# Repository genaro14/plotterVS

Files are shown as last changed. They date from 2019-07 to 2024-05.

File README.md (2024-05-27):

# plotterVS
This repository documents Pen plotter desing and usage.

## Background

I´ve been using DIY pen plotters for a while, 3d printed mostly, they were a lot of fun, but those lack of being reliable. This model it's my 2nd iteration trying to solve that issue and wanting to get a good quality final product, based on my particular needs and understanding of the "best" desing that fits the purpose but keeping the costs as low as possible. 
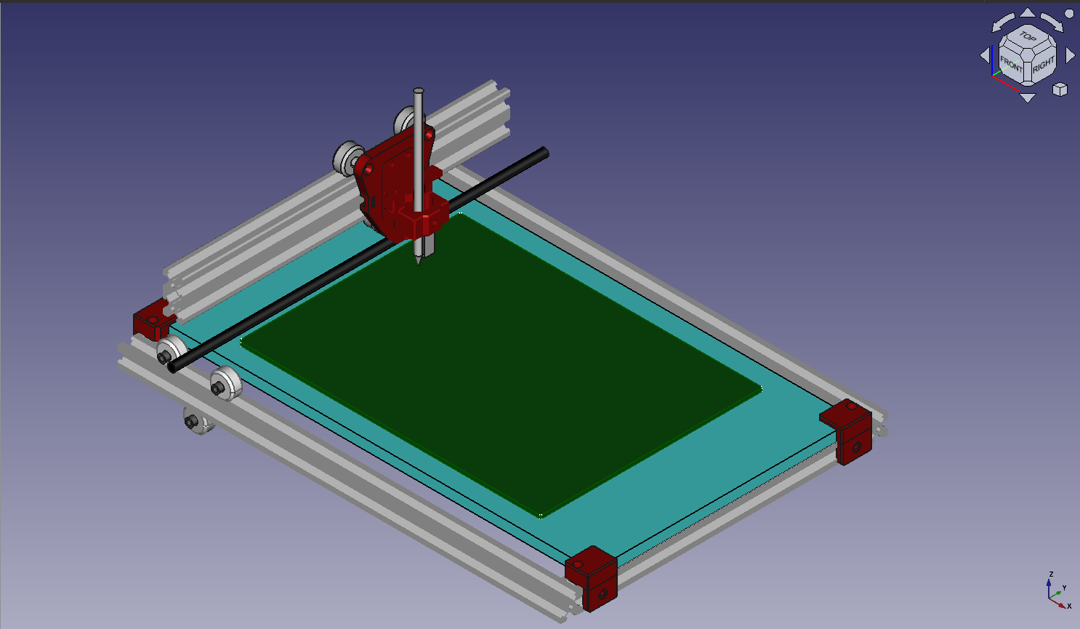
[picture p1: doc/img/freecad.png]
Desing


## How to - BASICS

You will convert a vector ( .SVG ) file to something the plotter can understand, a set of instructions listed in an .Gcode file.

`SVG >>> GCODE`

With a tool like: [SVG2GCODE](https://sameer.github.io/svg2gcode/), you can parse svg files to gcode.     
[Settings JSON file](./Plotter/clean/svg2gcode/svg2gcode_settings.json)   

See below fot templates.(SVG Templates)

Once the gcode file is ready you will send it to plotter. I won't go deeper in this subject.    
Plug >> Connect >> send the file and start it. Check each program docs for details.

Control software examples:
+ Universal Gcode Sender. [UGS](https://winder.github.io/ugs_website/) 
+ CNCJS [cncjs](https://cnc.js.org/)
+ GRBL- Plotter
+ Candle
+ Bcnc

Personally, I've been using the CNCJs over a Raspberry so i don´t need to wire my laptop, it's based on web interface and has proven to be stable and perfectly functional.

## SVG Templates
Some templates can be found in the this [folder](./Plotter/clean/templates).

## Part list for A4 size:
* 2040 vslot: x1 285mm
* 2020 vslot: x2 285mm, .x2 440mm
* Aluminum Corners: x4
* V wheels 22mm: x9 
* Wheel spacers: x6
* Eccentric nuts: x3
* Bolts & T Nuts: At least 12 each
* Gt2 pulleys: 1x 5mm, 2x 8mm
* Gt2 belt. 2 x 500mm, 1 x 600mm
* Gt2 freewheel. 3mm
* 8mm rod, at least 360mm
* Motors Nema 17 x2
* Servo G90
* Aruino Nano & Nanoshield CNC clone with A4988 drivers  (see below)
* Glass: 285 x 440 x 6mm (tempered would be better, but it's expensive, wood can be used too)

Firmware: [GRBL Servo by Misan](https://github.com/misan/grbl-servo) or Robottini's [GRBL Servo](https://github.com/robottini/grbl-servo).

Arduino case: [Link](https://www.thingiverse.com/thing:2379541)

Pen Holder: [Link](https://www.thingiverse.com/thing:3810653/files)

Desing [Freecad Files](./Plotter/2024/2024_complete.FCStd)

## Code Snippets
Code repository for plotting
### Python 
+ Fake cyrcle   
[Circle of Lines](./code/python/fakeCircle/fakeCircle.md).
+ L Systems   
[Lindenmayer Systems](./code/python/lindenmayerSystems/lindenmayerSystems.md)

## JS
+ ARchimendian Spirals    
[Triangle](./code/js/walk/Archimedian_forms/triangle.js)    
[Hexagon](./code/js/walk/Archimedian_forms/hexagon.js)    

### GRBL SERVO SETUP

[Library CODE](https://github.com/robottini/grbl-servo).
  GRBL 0.9i with servo motor support.     
  **Use the PIN D11 to drive the servo.**     
  Use the commands `M03 Sxxx` (xxx between 0 and 255) to rotate the servo between 0-180. The command ``M05`` turn the servo to zero degrees.
  On the current configuration for this build. `M03 S30` is enough for lifting the pen up and clearing the page.
  Commands `M3` and `M5` are valid too.   

| Code | Action  |
|---|---|
| M05 | Pen Down|
| M3 S30 | Pen Up  |

Example configuration can be found on:
[GRBL config](./Plotter/clean/grbl/grbl_config.md)
See below details to map proper pins

### Nanoshield Clone Fixes 
The cheapest controller board on hand was a Keyes Nanoshield clone that supports Arduino nano but it needs some work to work properly.

Soldering required!   
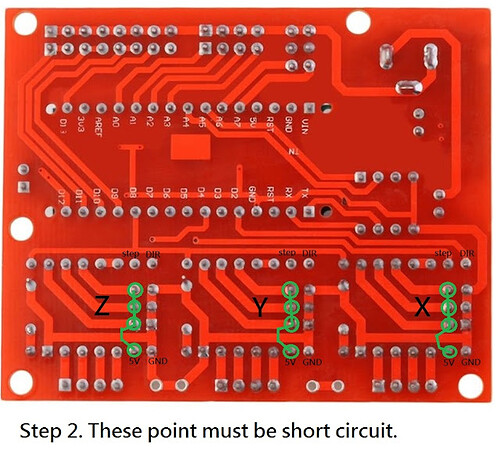
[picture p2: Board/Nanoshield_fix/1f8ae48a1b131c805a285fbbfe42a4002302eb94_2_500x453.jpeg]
Hardware
.    
Also before uploading GRBL to the board, the file 'cpu_map_atmega328.p' has to be modified or replaced.   
Grbl patch [here](./Board/Nanoshield_fix/cpu_map_atmega328p.h)    
Full details from [Instructables](https://www.instructables.com/Fix-Cloned-Arduino-NANO-CNC-Shield/)

## Results 
Cncjs Example and result:
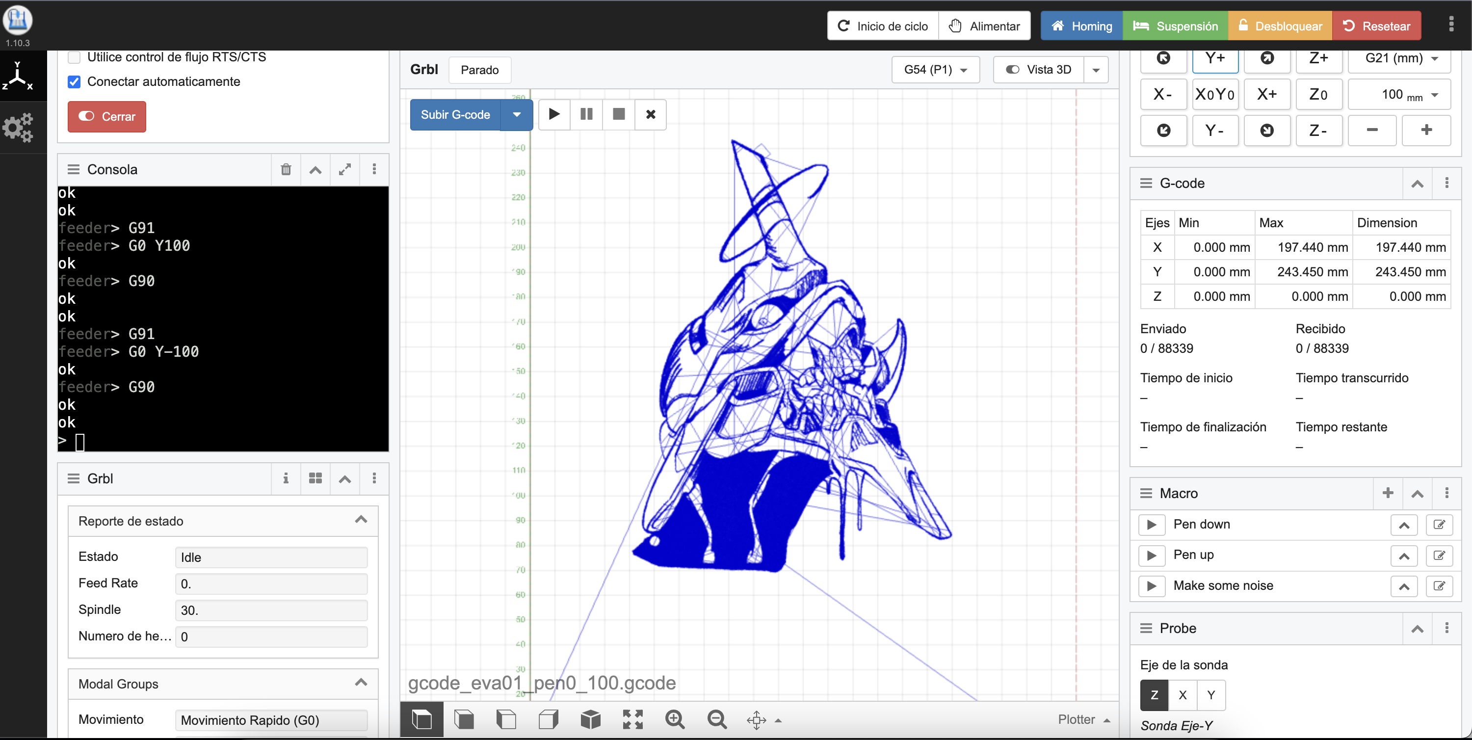
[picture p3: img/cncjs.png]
cncJs
 
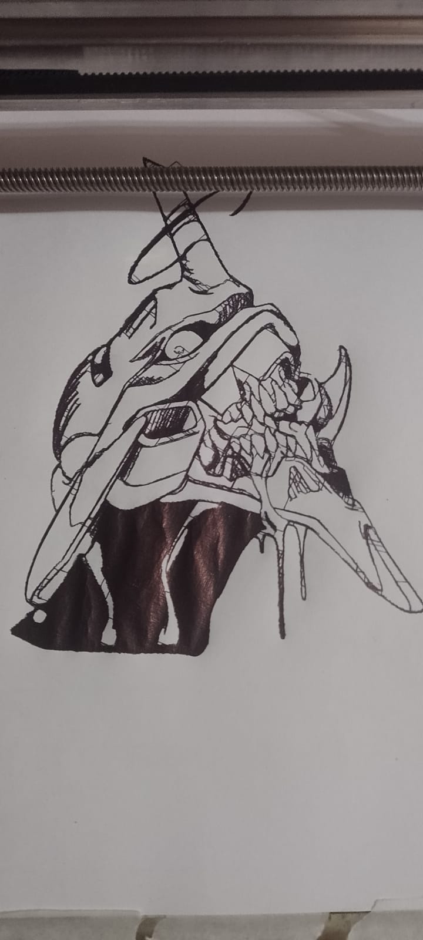
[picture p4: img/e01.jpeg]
eva
        

### Other:
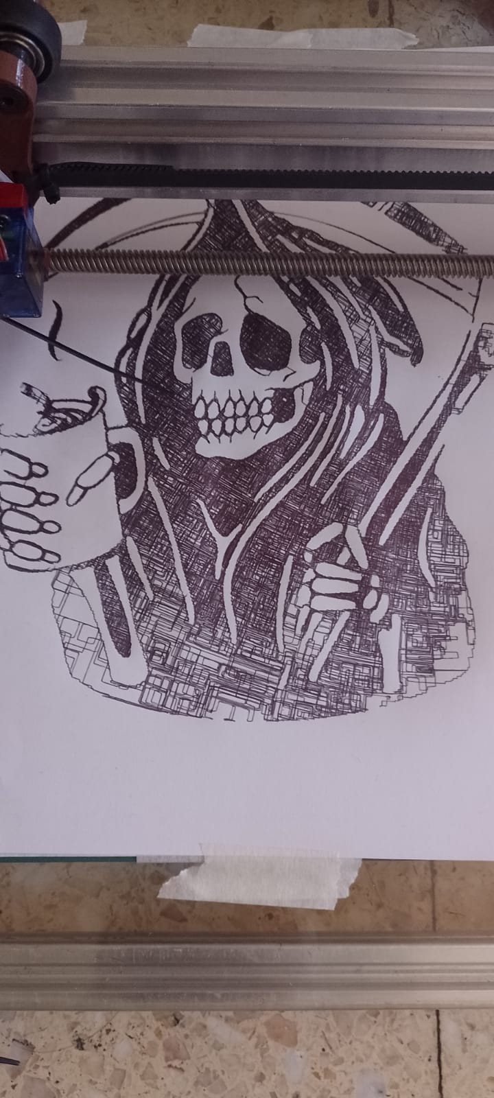
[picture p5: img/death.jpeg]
death
        
[View More](./img/)

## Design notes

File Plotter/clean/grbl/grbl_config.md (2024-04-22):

# GRBL CONFIG
Call to view settings: `$$`
``` bash
> $$
$0=10 (step pulse, usec)
$1=25 (step idle delay, msec)
$2=0 (step port invert mask:00000000)
$3=0 (dir port invert mask:00000000)
$4=0 (step enable invert, bool)
$5=0 (limit pins invert, bool)
$6=0 (probe pin invert, bool)
$10=3 (status report mask:00000011)
$11=0.010 (junction deviation, mm)
$12=0.002 (arc tolerance, mm)
$13=0 (report inches, bool)
$20=0 (soft limits, bool)
$21=0 (hard limits, bool)
$22=0 (homing cycle, bool)
$23=0 (homing dir invert mask:00000000)
$24=25.000 (homing feed, mm/min)
$25=500.000 (homing seek, mm/min)
$26=250 (homing debounce, msec)
$27=1.000 (homing pull-off, mm)
$100=80.000 (x, step/mm)
$101=80.000 (y, step/mm)
$102=250.000 (z, step/mm)
$110=25000.000 (x max rate, mm/min)
$111=10000.000 (y max rate, mm/min)
$112=500.000 (z max rate, mm/min)
$120=1000.000 (x accel, mm/sec^2)
$121=500.000 (y accel, mm/sec^2)
$122=10.000 (z accel, mm/sec^2)
$130=220.000 (x max travel, mm)
$131=300.000 (y max travel, mm)
$132=200.000 (z max travel, mm)
```

## Setting
For each one: set key=value

`$110=25000`

## Changes record

Date: 13/04/2024.     
````bash
$111=9000
$121=400.000
````

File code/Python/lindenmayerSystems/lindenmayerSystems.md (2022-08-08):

# Lindenmayer systems

Lindenmayer systems, or L-systems, provide a very powerful way to construct fractals. Lindenmayer used L-systems to describe the behaviour of plant cells and to model the growth processes of plant development. An L-system is a rewriting system and a type of formal grammar. It consists of an alphabet of symbols that can be used to make strings, a collection of production rules that expand each symbol into some larger string of symbols, an initial “axiom” string from which to begin construction, and a mechanism for translating the generated strings into geometric structures.

For a simple example, let’s look at Lindenmayer’s original L-system for modelling the growth of algae. There are 2 ‘variables’, A and B. The rules are that (1) whenever we see A, we replace it with AB, and (2) whenever we see B, we replace it with A. We start with the string ‘A’, so that becomes ‘AB’ by rule 1. There’s nothing more in the original string, so now we scan ‘AB’. Again, the ‘A’ gets replaced by ‘AB’, and we move on to the next character, which is ‘B’; that gets replaced by ‘A’ so now the string has become ‘ABA’. On our third iteration, the string becomes ‘ABAAB’. The next one is ‘ABAABABA’. And so on. (Just as a side note, the lengths of these string are 1, 2, 3, 5, 8… remind you of anything? Hint, put another ‘1’ at the beginning of the sequence, and add it to the next number.)

We can extend this basic system with some drawing instructions, such as ‘-‘ means “turn left by some angle”, and ‘+’ indicates a right turn; ‘F’ could say “go forward”. These instructions can then be implemented very simply using Turtle graphics. For example, the Hilbert curve can be drawn using these rules:

A → − B F + A F A + F B −

B → + A F − B F B − F A +

``` python
#   Hilbert curve using L-system
#   Authour: Alan Richmond, Python3.codes
#   https://en.wikipedia.org/wiki/L-system
#   Uses Lindenmayer System

from turtle import*

def A(n):
    if n>0:    L("-BF+AFA+FB-",n)

def B(n):
    if n>0:    L("+AF-BFB-FA+",n)

def L(s,n):
    for c in s:
        if   c=='-': lt(90)
        elif c=='+': rt(90)
        elif c=='A': A(n-1)
        elif c=='B': B(n-1)
        elif c=='F': fd(9)

penup();goto(0,100);pendown()
A(4)
```
A note about the implementation: this one is remarkably simple because we do the string replacements ‘on-the-fly’ with mutually recursive function calls. You’ll often see L-systems implemented by scanning the axiom (usually the first production rule) and building up the replacement string, and then scanning that, and so on until the string has been developed as far as needed. Then that string is ‘interpreted’ (like a little programming language!) to draw the picture. I’m not sure why they do that – presumably there’s a good reason? – but my way is much easier to understand!

Here’s a Dragon Curve:

``` python
#   Dragon curve using L-system
#   Authour:Alan Richmond, Python3.codes
#   https://en.wikipedia.org/wiki/L-system

from turtle import*

def X(n):
    if n>0:    L("X+YF+",n)
def Y(n):
    if n>0:    L("-FX-Y",n)

def L(s,n):
    for c in s:
        if   c=='-': lt(90)
        elif c=='+': rt(90)
        elif c=='X': X(n-1)
        elif c=='Y': Y(n-1)
        elif c=='F': fd(16)

X(8)

```

This next one adds a new feature – the ability to save values for future use, by pushing them onto a stack, and popping them off later. Push is indicated by ‘[‘, and pop by ‘]’. I hope you can see that there’s the beginnings of a realistic looking tree when the program has finished! Just add some scenery and textures…?

``` Python
#   Fractals using L-system
#   Authour:Alan Richmond, Python3.codes
#   https://en.wikipedia.org/wiki/L-system

from turtle import*
#from random import gauss

t=22                    # angle of branches
d=16                    # length of branches
n=4                     # max depth of recursion

X="F-[[X]+X]+F[+FX]-X"  # Lindenmayer system
F="F"

stack=[]

def x(n):
    if n>0: L(X,n)
    else:   dot(16,'green')

def f(n):
    if n>0: L(F,n)

def L(s,n):
    pensize(n*2)
    for c in s:

#        if   c=='-':    lt(gauss(t,t))
#        elif c=='+':    rt(gauss(t,t))
        if   c=='-':    lt(t)
        elif c=='+':    rt(t)
        elif c=='X':    x(n-1)
        elif c=='F':    f(n-1);fd(d)
        elif c=='[':    stack.append((pos(),heading(),n))
        elif c==']':
            ((i,j),h,p)=stack.pop()
            penup()
            goto(i,j)
            seth(h)
            pensize(p)
            pendown()

penup()
goto(0,-200)
pendown()
seth(90)
color('brown','green')
x(n)
```

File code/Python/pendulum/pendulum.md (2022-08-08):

# Pendulum

This is a simple harmonograph simulator to generate random-ish harmonographs. It asks for the number of pendulums, and exits if the number is 0. It also asks for the frequency spread, which means roughly, how far from integer may the frequencies go. The nearer to integer they are, the ‘cleaner’ looking the harmonographs are, but they tend to be perhaps less interesting. The further from integer they are, the more they’re likely to look messy.

If you’ve seen harmonograph programs before you might expect there to be an outer loop for stepping through the ‘time’ variable. That’s not necessary here because numpy handles it for us, making the program simpler and much faster. The outer loop here gets user input and generates random parameters for each pendulum’s oscillation (i.e. sine wave): amplitude, frequency, and phase. The one inner loop computes, for each pendulum, the whole x and y vectors, at once. That is, numpy notices that ‘t’ is a vector and so knows to compute x and y using faster code than Python (C).

Each picture is drawn in its own window, which remains on screen until the program exits, or you dismiss it. This way, you can compare several pictures and select the best if you want to keep some. To save a picture, click on the floppy disc icon on the window’s menu bar. Note that the image size depends on the window size you saved it from. To get a bigger picture (or smaller), first adjust the window size.

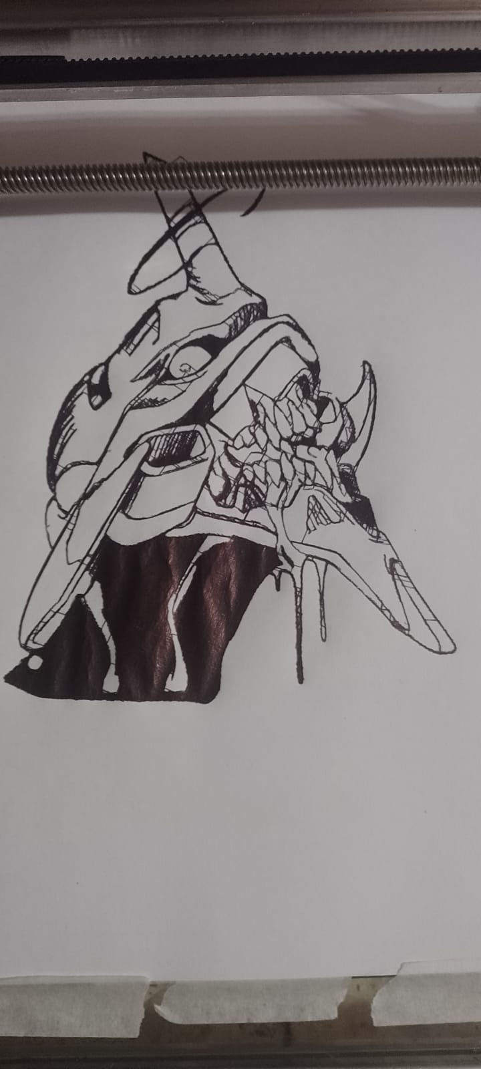
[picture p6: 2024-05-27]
img/exa4.jpeg

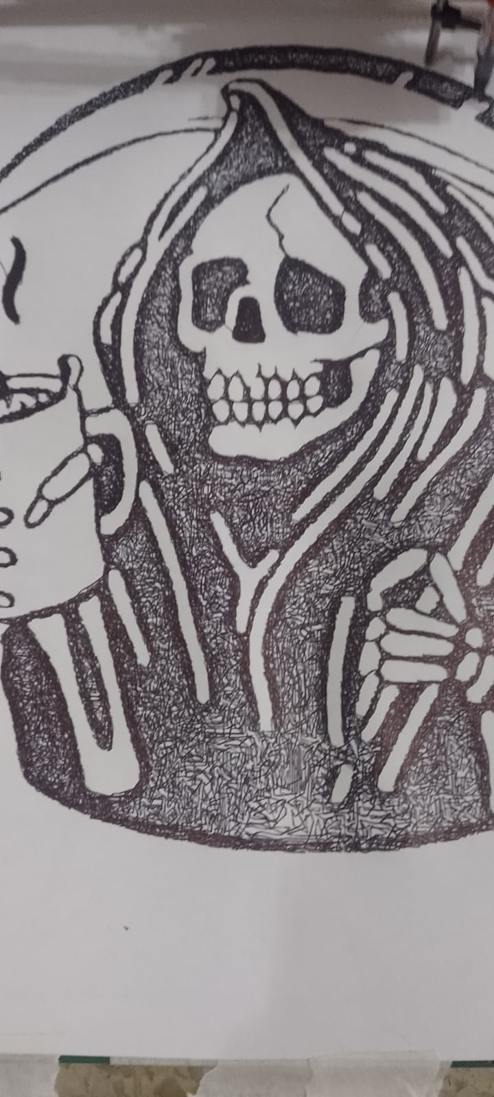
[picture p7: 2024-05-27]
img/exa3.jpeg

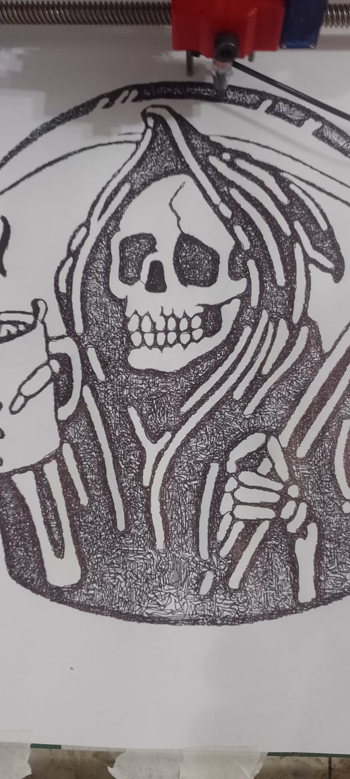
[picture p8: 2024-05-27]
img/exa5.jpeg

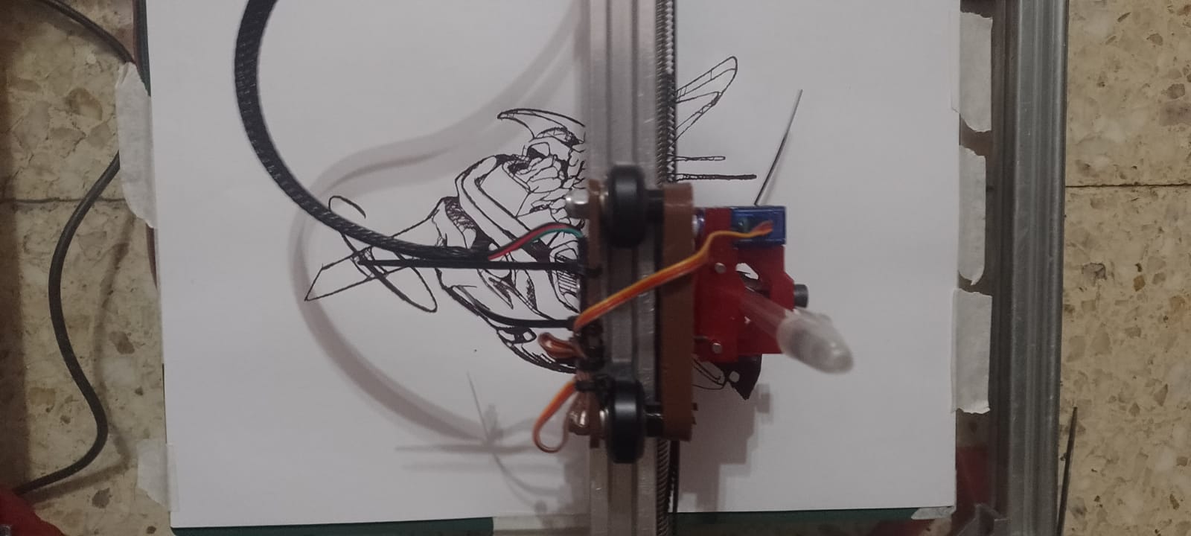
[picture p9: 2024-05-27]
img/exa2.jpeg

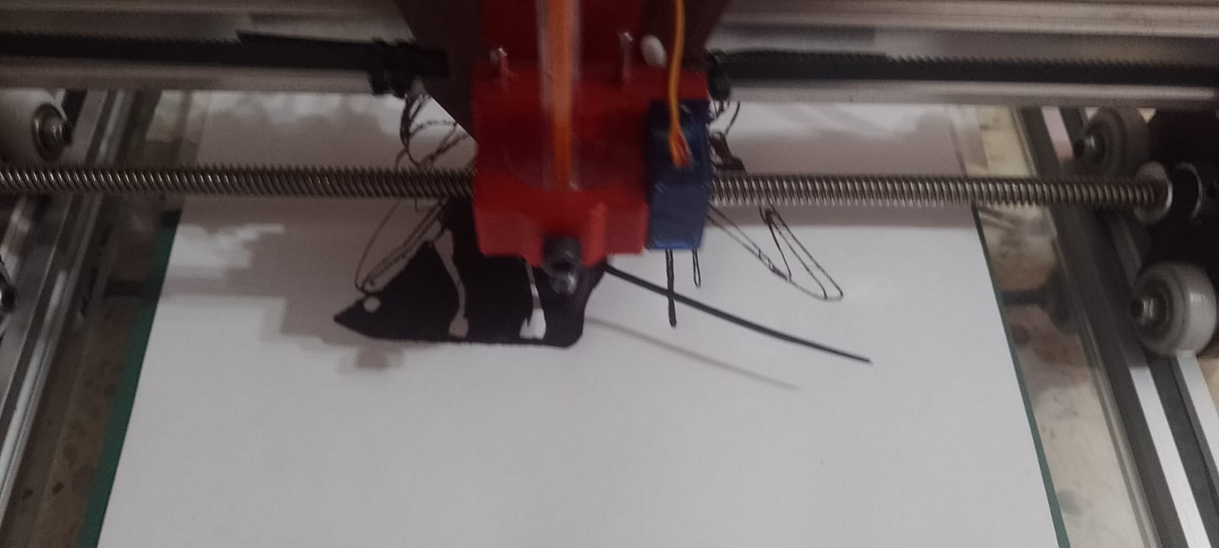
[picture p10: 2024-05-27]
img/example1.jpeg

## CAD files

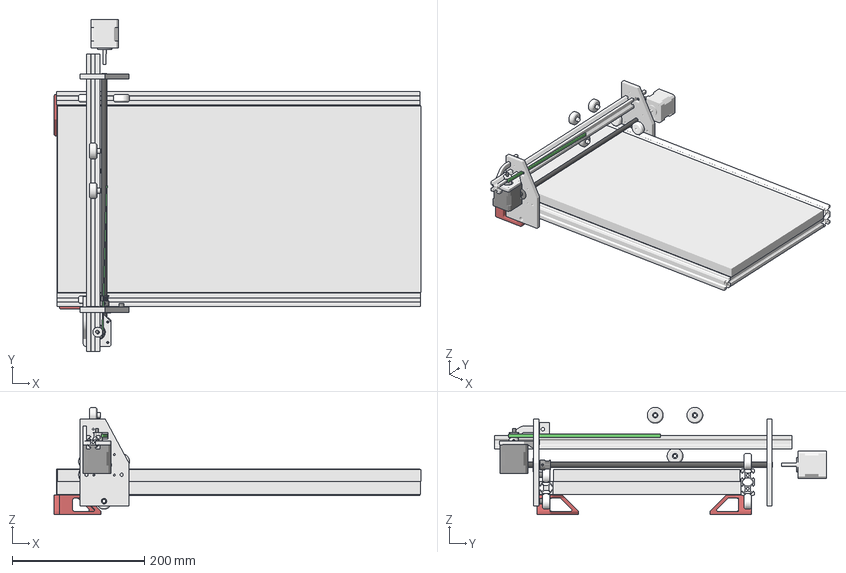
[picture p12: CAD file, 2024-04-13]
Plotter/2024/2024_complete.FCStd
555.2 x 501.9 x 162.4 mm
LadoA
LadoB
LadoC
wheelL1
WheelL3
SpacerL3
SpacerL1
SpacerL2
eje8
bearingL_608zz
A4 Mat
wheel002
wheel001
wheel
GT2
spacer005
spacer006
spacer007
WheelL004
wheelL002
WheelL005
GT2_20T_Y_axis
Foot002
Foot003
Yaxis_motor
X_MOTOR2
GT2_20T_pulley_x
Xaxis_motor
2024_Y_axis-2040_550
2020_v-slot_profile_450

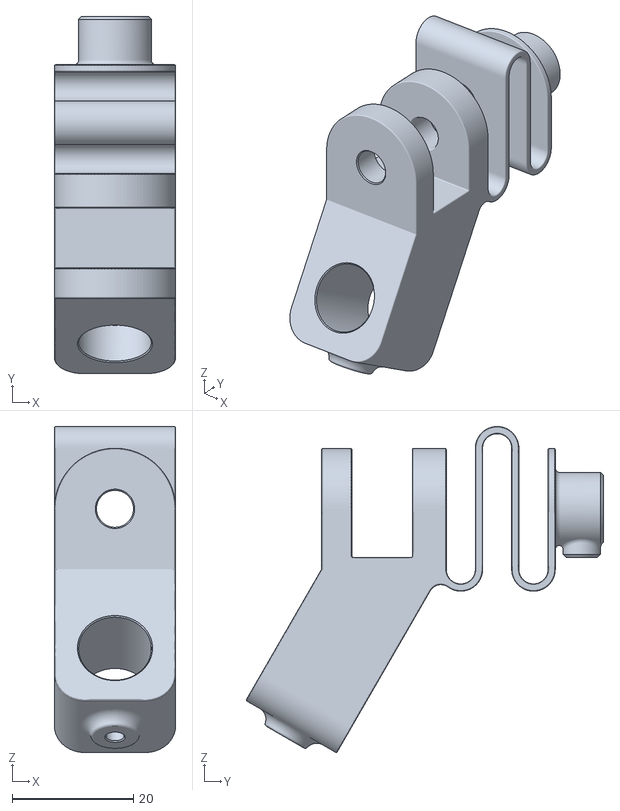
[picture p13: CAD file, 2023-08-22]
Plotter/Sort/Pen Holder/CNC_Pen_Holder_main_body.stl
20.0 x 59.0 x 53.8

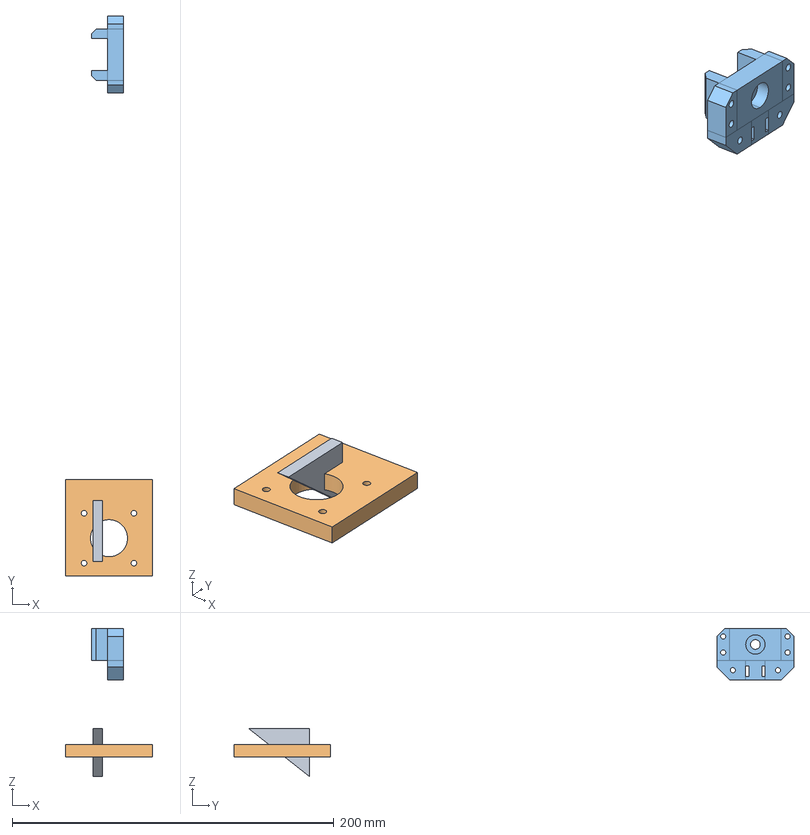
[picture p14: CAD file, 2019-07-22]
files/v2.FCStd
54.0 x 348.0 x 92.1 mm
Pad002Body
Pad001Body

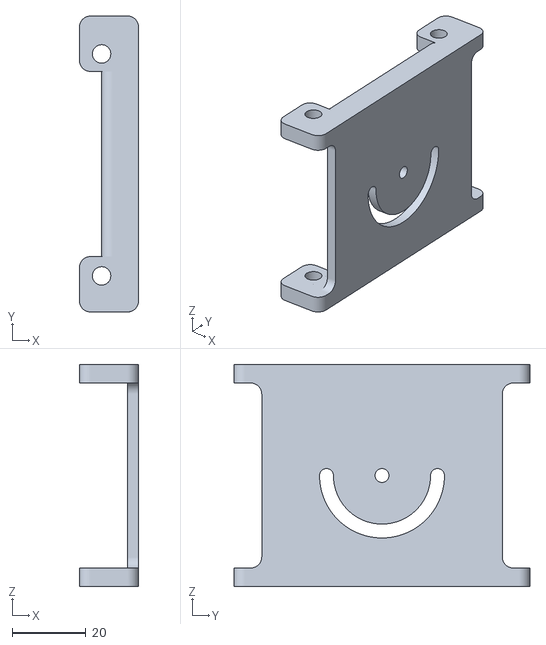
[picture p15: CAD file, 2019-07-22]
parts/portaPen.stl
16.0 x 80.0 x 60.0

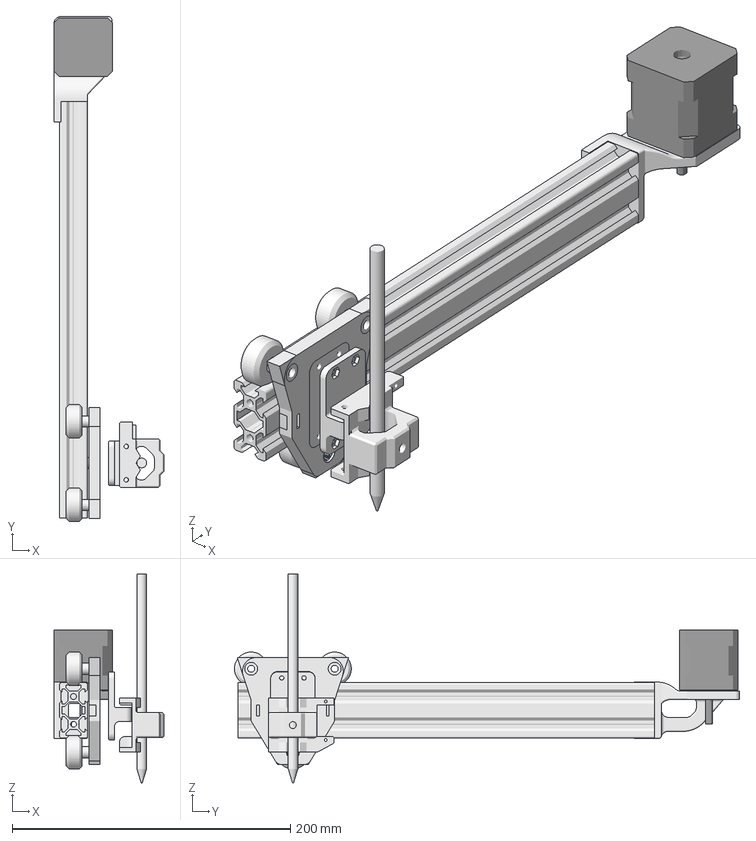
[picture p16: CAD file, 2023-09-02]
Plotter/2024/X_Axis/X_AXIS.FCStd
79.0 x 363.0 x 150.0 mm
wheel01
wheel02
wheel03
spacer01
spacer02
spacer03
Pen_tip001
X_axis_carriage
2040_perrfil
Soporte_Motor_X
Motor_X001
P1
P2

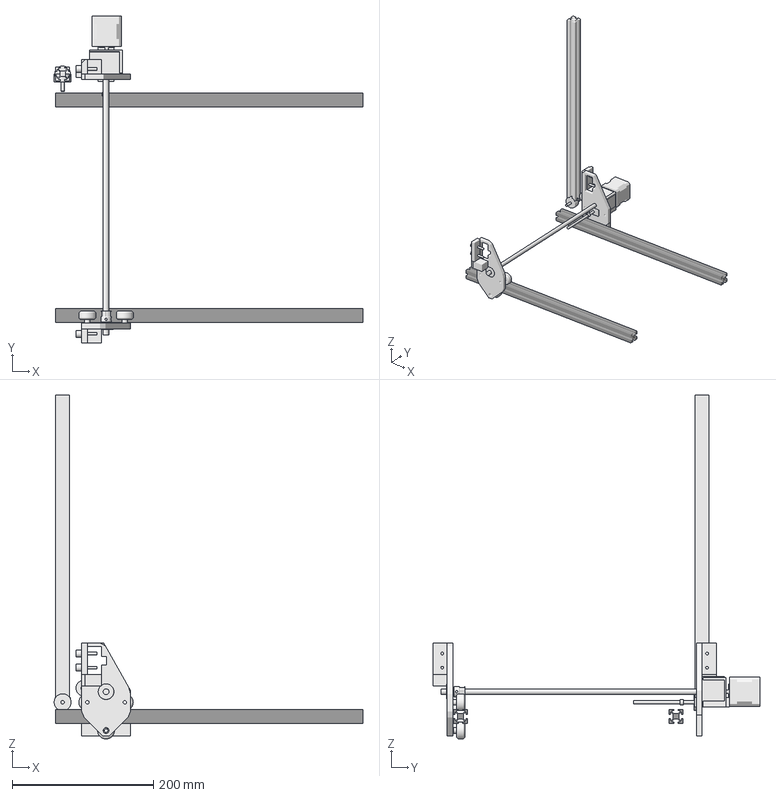
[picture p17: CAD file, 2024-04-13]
Plotter/2024/Y_Axis/Y_Axis.FCStd
437.0 x 462.9 x 487.0 mm
Lado B
Lado C
Y_Axis_Master
Cilindro011
Cilindro012
Cilindro014
Cilindro013
Cubo025
Cilindro010
Cilindro015
Cubo026
Y_AXIS_Master01
bearing002
wheel3
wheel001
axis007
axis006
Real_wheel006
Real_wheel007
spacer001
spacer002
wheel002
axis008
Real_wheel008
spacer010
bearing001
bearing
Cilindro007
Cilindro008
Y_AXIS_Master002
Y_Axis_Master002
eje8
Y_AXIS_A
Cilindro016
Cilindro017
Cilindro018
Cilindro019
Cubo
Pad008Body
Pad007Body
Pad005Body
Cubo028
Cubo029
Yaxis
GT2_20T_Y_axis

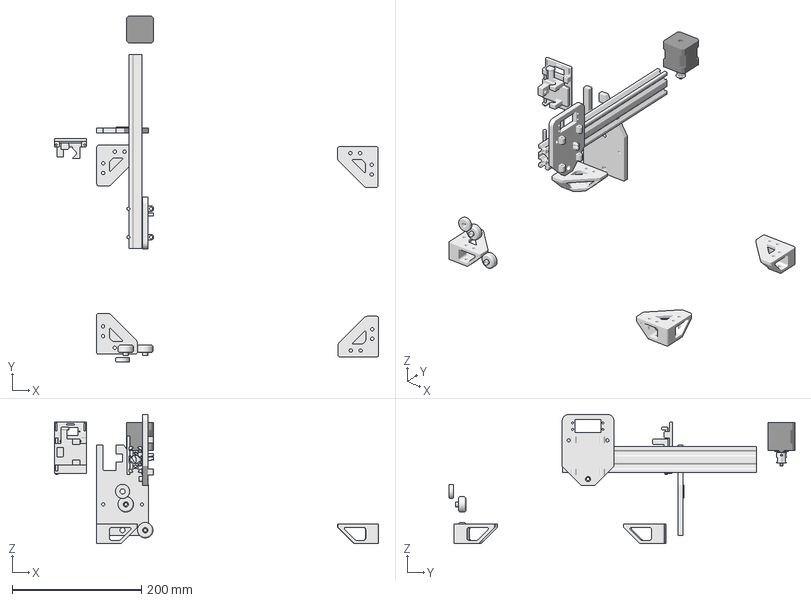
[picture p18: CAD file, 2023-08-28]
Plotter/Complete/ploter23.FCStd
501.6 x 535.0 x 199.6 mm
spacer005
Cilindro001
Cilindro002
bearing
bearing001
spacer008
spacer009
Cilindro009
2040_long001
Xaxis
GT2_20T_dzino
Foot
Foot001
Foot002
Foot003
pen_mount
servo_mount

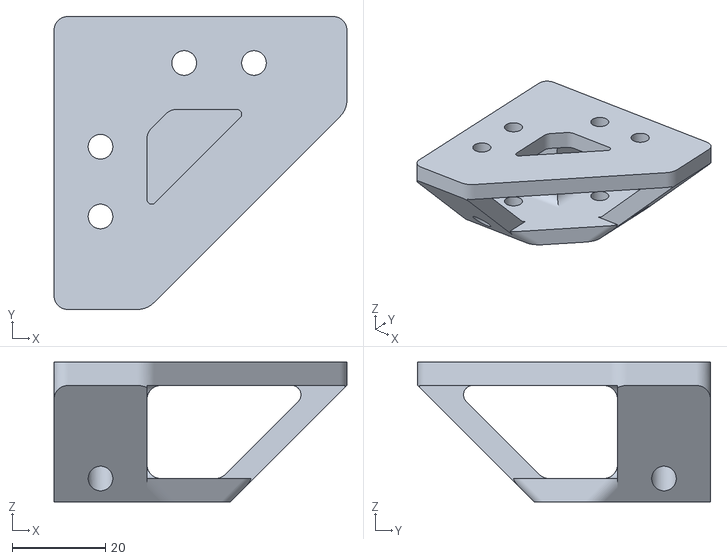
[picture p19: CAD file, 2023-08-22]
Plotter/Sort/2020_Extrusion_Foot__30mm_tall__2068704/Foot.stl
63.0 x 63.0 x 30.0

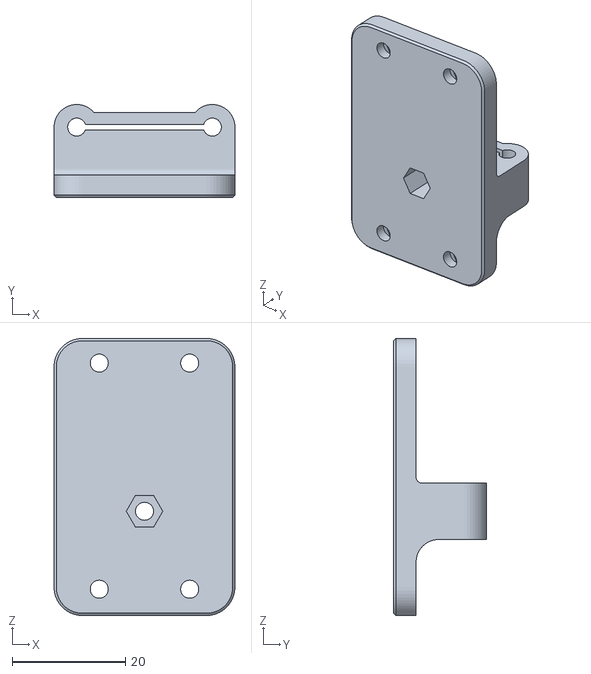
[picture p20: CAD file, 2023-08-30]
Plotter/Sort/Pen Holder/P1.stl
32.0 x 16.4 x 49.0

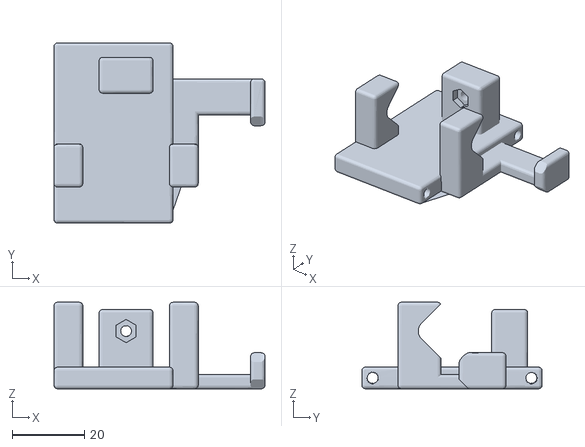
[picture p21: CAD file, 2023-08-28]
Plotter/Sort/slider_3mm_rod_holes.stl
58.5 x 50.0 x 24.0

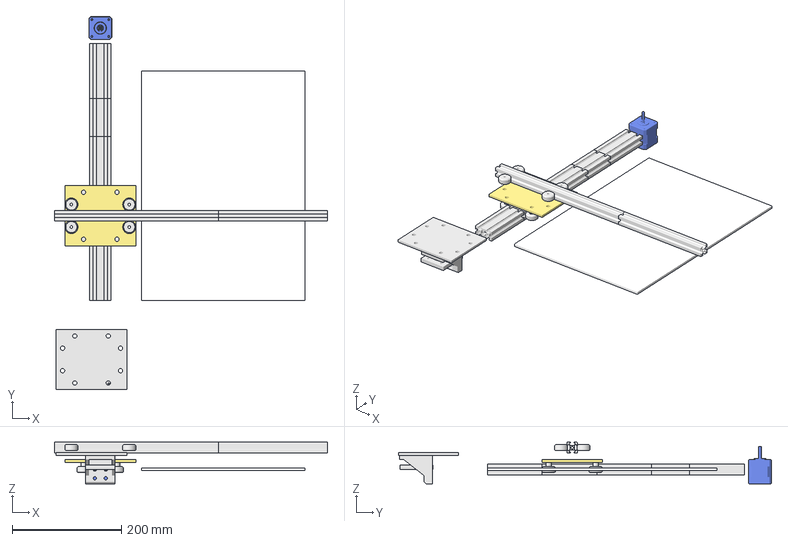
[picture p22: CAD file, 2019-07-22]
files/plotter_pro.FCStd
500.0 x 682.8 x 76.0 mm
2020-2040-corner v1
2020-2040-corner v002
2020-2040-corner v003
2020-2040-corner v004
2020-2040-corner v005
2020-2040-corner v006
2020-2040-corner v007
2020-2040-corner v008
2040_100mm
2040_100mm001
2040_100mm003
2040_100mm004
2040_100mm005
2020 alu section
2020 alu section001
NEMA 17

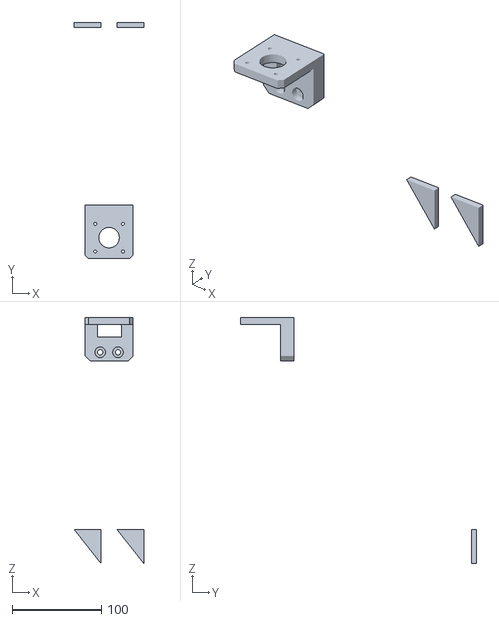
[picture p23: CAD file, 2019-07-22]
parts/nema_support.stl
78.0 x 265.0 x 275.9

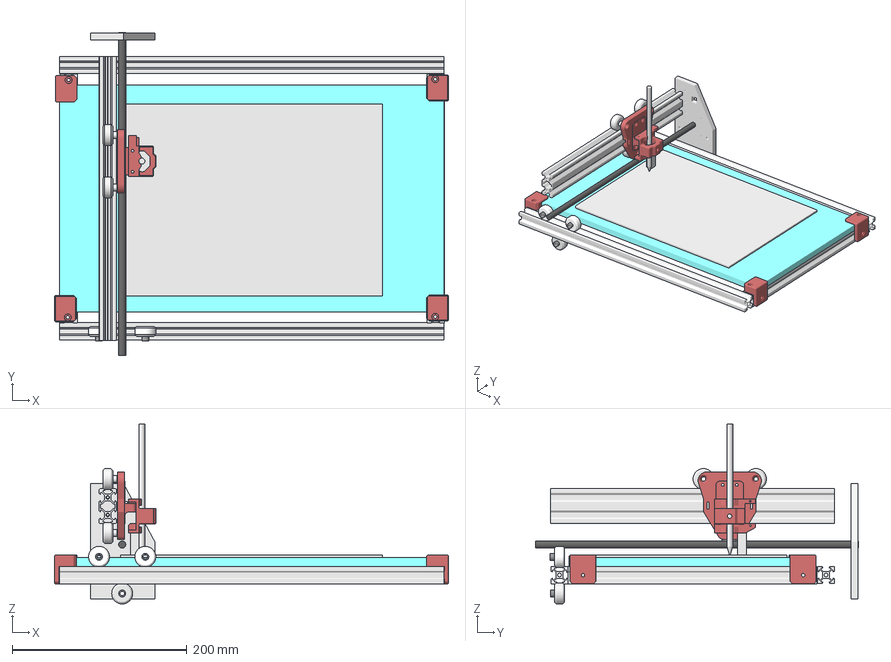
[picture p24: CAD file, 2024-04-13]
Plotter/2024/Y_Axis/2024_Y_axis.FCStd
451.0 x 370.0 x 206.0 mm
wheelL1
WheelL3
SpacerL3
SpacerL1
WheelL2
SpacerL2
eje8
A4 Mat
wheel002
wheel001
wheel
spacer005
spacer006
spacer007
X_axis_carriage
Pen_tip001
Glass
Corner_F_R001
Corner_R_L
Corner_F_R
Y_axis-2040
Side_R_2020_v-slot_profile_440
Side_L_2020_v-slot_profile_440
Side_R_2020_v-slot_profile_285
Lado_F_2020_v-slot_profile_285
Pen_holder_1
Pen_holder_2

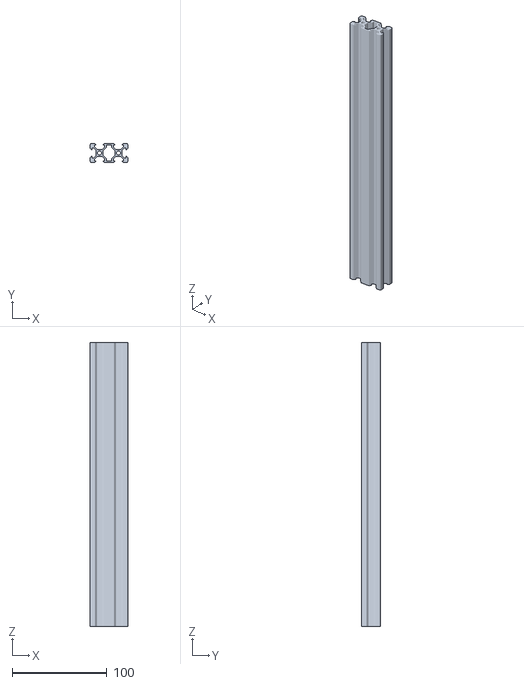
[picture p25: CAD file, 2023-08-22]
Plotter/Sort/2040_long.stl
40.0 x 20.0 x 300.0

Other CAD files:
Plotter/Sort/Pen Holder/P2.stl
parts/portaServo.stl
Plotter/Sort/GT2_20T_dzino.STL
Plotter/Sort/Pen Holder/pen_mount.stl
Cantilever_deprecated/files/penside_6mm.FCStd
Cantilever_deprecated/parts/end_penside.stl
Cantilever_deprecated/parts/end_pulley side.stl
Cantilever_deprecated/parts/portaServo.stl
Plotter/Sort/2040.stl
Plotter/Sort/Pen Holder/PEN_HOLDER_MOD.stl
Plotter/Sort/Pen Holder/PEN_HOLDER_MOD_compact.stl
Plotter/Sort/Pen Holder/Pen_holder_spring.stl
Plotter/Sort/Pen Holder/Pen_holder_spring_6mm.stl
Plotter/Sort/VSLOT_Mini_V_Plate.stl
Plotter/Sort/s3003-servo-arm.stl
Plotter/Sort/s3003-servo.stl
parts/end_penside.stl
parts/end_pulley side.stl

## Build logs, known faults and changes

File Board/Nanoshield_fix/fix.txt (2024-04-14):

https://www.instructables.com/Fix-Cloned-Arduino-NANO-CNC-Shield/

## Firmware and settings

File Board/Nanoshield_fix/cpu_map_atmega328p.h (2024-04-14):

/*
  cpu_map_atmega328p.h - CPU and pin mapping configuration file
  Part of Grbl

  Copyright (c) 2012-2015 Sungeun K. Jeon

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
  You should have received a copy of the GNU General Public License
  along with Grbl.  If not, see <http://www.gnu.org/licenses/>.
*/

/* Grbl officially supports the Arduino Uno, but the other supplied pin mappings are
   supplied by users, so your results may vary. This cpu_map file serves as a central
   pin mapping settings file for AVR 328p used on the Arduino Uno.  */
   
#ifdef GRBL_PLATFORM
#error "cpu_map already defined: GRBL_PLATFORM=" GRBL_PLATFORM
#endif


#define GRBL_PLATFORM "Atmega328p"

// Define serial port pins and interrupt vectors.
#define SERIAL_RX     USART_RX_vect
#define SERIAL_UDRE   USART_UDRE_vect

// Define step pulse output pins. NOTE: All step bit pins must be on the same port.
#define STEP_DDR        DDRD
#define STEP_PORT       PORTD
#define X_STEP_BIT      5  // Uno Digital Pin 2
#define Y_STEP_BIT      6  // Uno Digital Pin 3
#define Z_STEP_BIT      7  // Uno Digital Pin 4
#define STEP_MASK       ((1<<X_STEP_BIT)|(1<<Y_STEP_BIT)|(1<<Z_STEP_BIT)) // All step bits

// Define step direction output pins. NOTE: All direction pins must be on the same port.
#define DIRECTION_DDR     DDRD
#define DIRECTION_PORT    PORTD
#define X_DIRECTION_BIT   2  // Uno Digital Pin 5
#define Y_DIRECTION_BIT   3  // Uno Digital Pin 6
#define Z_DIRECTION_BIT   4  // Uno Digital Pin 7
#define DIRECTION_MASK    ((1<<X_DIRECTION_BIT)|(1<<Y_DIRECTION_BIT)|(1<<Z_DIRECTION_BIT)) // All direction bits

// Define stepper driver enable/disable output pin.
#define STEPPERS_DISABLE_DDR    DDRB
#define STEPPERS_DISABLE_PORT   PORTB
#define STEPPERS_DISABLE_BIT    0  // Uno Digital Pin 8
#define STEPPERS_DISABLE_MASK   (1<<STEPPERS_DISABLE_BIT)

// Define homing/hard limit switch input pins and limit interrupt vectors. 
// NOTE: All limit bit pins must be on the same port, but not on a port with other input pins (CONTROL).
#define LIMIT_DDR        DDRB
#define LIMIT_PIN        PINB
#define LIMIT_PORT       PORTB
#define X_LIMIT_BIT      1  // Uno Digital Pin 9
#define Y_LIMIT_BIT      2  // Uno Digital Pin 10
#ifdef VARIABLE_SPINDLE // Z Limit pin and spindle enabled swapped to access hardware PWM on Pin 11.  
  #define Z_LIMIT_BIT	   4 // Uno Digital Pin 12
#else
  #define Z_LIMIT_BIT    3  // Uno Digital Pin 11
#endif
#define LIMIT_MASK       ((1<<X_LIMIT_BIT)|(1<<Y_LIMIT_BIT)|(1<<Z_LIMIT_BIT)) // All limit bits
#define LIMIT_INT        PCIE0  // Pin change interrupt enable pin
#define LIMIT_INT_vect   PCINT0_vect 
#define LIMIT_PCMSK      PCMSK0 // Pin change interrupt register

// Define spindle enable and spindle direction output pins.
#define SPINDLE_ENABLE_DDR    DDRB
#define SPINDLE_ENABLE_PORT   PORTB
// Z Limit pin and spindle PWM/enable pin swapped to access hardware PWM on Pin 11.
#ifdef VARIABLE_SPINDLE 
  #ifdef USE_SPINDLE_DIR_AS_ENABLE_PIN
    // If enabled, spindle direction pin now used as spindle enable, while PWM remains on D11.
    #define SPINDLE_ENABLE_BIT    5  // Uno Digital Pin 13 (NOTE: D13 can't be pulled-high input due to LED.)
  #else
    #define SPINDLE_ENABLE_BIT    3  // Uno Digital Pin 11
  #endif
#else
  #define SPINDLE_ENABLE_BIT    4  // Uno Digital Pin 12
#endif
#ifndef USE_SPINDLE_DIR_AS_ENABLE_PIN
  #define SPINDLE_DIRECTION_DDR   DDRB
  #define SPINDLE_DIRECTION_PORT  PORTB
  #define SPINDLE_DIRECTION_BIT   5  // Uno Digital Pin 13 (NOTE: D13 can't be pulled-high input due to LED.)
#endif
  
// Define flood and mist coolant enable output pins.
// NOTE: Uno analog pins 4 and 5 are reserved for an i2c interface, and may be installed at
// a later date if flash and memory space allows.
#define COOLANT_FLOOD_DDR   DDRC
#define COOLANT_FLOOD_PORT  PORTC
#define COOLANT_FLOOD_BIT   3  // Uno Analog Pin 3
#ifdef ENABLE_M7 // Mist coolant disabled by default. See config.h to enable/disable.
  #define COOLANT_MIST_DDR   DDRC
  #define COOLANT_MIST_PORT  PORTC
  #define COOLANT_MIST_BIT   4 // Uno Analog Pin 4
#endif  

// Define user-control controls (cycle start, reset, feed hold) input pins.
// NOTE: All CONTROLs pins must be on the same port and not on a port with other input pins (limits).
#define CONTROL_DDR       DDRC
#define CONTROL_PIN       PINC
#define CONTROL_PORT      PORTC
#define RESET_BIT         0  // Uno Analog Pin 0
#define FEED_HOLD_BIT     1  // Uno Analog Pin 1
#define CYCLE_START_BIT   2  // Uno Analog Pin 2
#define SAFETY_DOOR_BIT   1  // Uno Analog Pin 1 NOTE: Safety door is shared with feed hold. Enabled by config define.
#define CONTROL_INT       PCIE1  // Pin change interrupt enable pin
#define CONTROL_INT_vect  PCINT1_vect
#define CONTROL_PCMSK     PCMSK1 // Pin change interrupt register
#define CONTROL_MASK ((1<<RESET_BIT)|(1<<FEED_HOLD_BIT)|(1<<CYCLE_START_BIT)|(1<<SAFETY_DOOR_BIT))
  
// Define probe switch input pin.
#define PROBE_DDR       DDRC
#define PROBE_PIN       PINC
#define PROBE_PORT      PORTC
#define PROBE_BIT       5  // Uno Analog Pin 5
#define PROBE_MASK      (1<<PROBE_BIT)

// Start of PWM & Stepper Enabled Spindle
#ifdef VARIABLE_SPINDLE
  // Advanced Configuration Below You should not need to touch these variables
  #define PWM_MAX_VALUE    255.0
  #define TCCRA_REGISTER	 TCCR2A
  #define TCCRB_REGISTER	 TCCR2B
  #define OCR_REGISTER     OCR2A
  
  #define COMB_BIT	     COM2A1
  #define WAVE0_REGISTER	 WGM20
  #define WAVE1_REGISTER	 WGM21
  #define WAVE2_REGISTER	 WGM22
  #define WAVE3_REGISTER	 WGM23
      
  // NOTE: On the 328p, these must be the same as the SPINDLE_ENABLE settings.
  #define SPINDLE_PWM_DDR	  DDRB
  #define SPINDLE_PWM_PORT  PORTB
  #define SPINDLE_PWM_BIT	  3    // Uno Digital Pin 11
#endif // End of VARIABLE_SPINDLE

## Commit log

2019-07-22 Repo init
    [end_penside.stl, end_pulley side.stl, nema_support.stl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]
2023-08-22 Cartesian plotter
    [2040.stl, 2040_long.stl, CNC_Pen_Holder_main_body.stl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]
2023-09-02 chore: Updates. Still need to clean
    [2040.stl, 2040_long.stl, CNC_Pen_Holder_main_body.stl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]
2023-09-02 chore: Cleanup
    [2040.stl, 2040_long.stl, CNC_Pen_Holder_main_body.stl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]
2024-04-13 2024 Update.
    [2024_Y_axis.FCStd, 2024_complete.FCStd, Profile_v1.scad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]

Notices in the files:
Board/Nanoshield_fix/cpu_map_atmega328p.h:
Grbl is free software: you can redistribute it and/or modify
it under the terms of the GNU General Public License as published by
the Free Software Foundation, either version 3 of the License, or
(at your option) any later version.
